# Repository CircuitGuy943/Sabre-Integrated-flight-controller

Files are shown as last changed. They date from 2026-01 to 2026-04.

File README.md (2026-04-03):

I am currently trying to build my own drone from scratch, and slowly replace every component with my own, from creating fully custom PCBs for the flight controller or ESCs, to making a 3D printed drone chassis etc etc. And this is the fully fledged, multi functional, cool-looking flight controller. I present to you:

# *SABRE!*




For one of my biggest projects yet I designed a jack of all trades custom flight controller board. It also comes with custom firmware, or if possible compatibility with betaflight or other FC firmware out there. At it's core are two PCBs arranged in a stackup with the "top" and "bottom" sections. The two PCBs connect through the common 2.54mm pitch headers and stack on top of eachother and each serve to provide enough space for all the components and separate the sensitive digital components from the electromagnetic potential of the motor power rails. The bottom board houses E-Fuse protection and an INA226 current monitor to protect the boards, including powered FPV feed with the AT7456E and TX5813, accompanied by four MOSFET powered 12V LED strip channels. The top booard houses a powerful STM32F765VGT CPU which will, *fingers crossed,* be more than enough to run automatic flight levelling software quickly enough to not crash. Followed by a micro SD card slot for storing flight telemetry, programmable DIP switched for easy settings, BNO08x 9-DOF sensor module, segment display and pushbuttons for easy configuration without needing to reupload code and a BMP580 barometic sensor. More than I (or you) will ever need to fly a 4 blade, 1KG piece of PETG plastic :)

### Bottom Board:

Half of the bottom PCB houses the power delivery circuitry. This includes a dedicated TPS259850 chip, or an E-Fuse, required protection option for a drone that operates at around 20A sustained and 40A current peaks. Thanks to it's extremely low RDS on, basically no power is wasted, and it trips the circuit in a matter of microseconds when too much current is detected, which makes it extremely useful for a drone full of sensitive circuitry, compared to a traditional wire fuse. Followed by that is an INA226 chip, this aims to precisely monitor the current consumption of the entire drone, helping to predict flight times and efficiently manage battery health, through the use of a shunt resistor sized to the expected current draw. The current planes are optimized to make proper use of the different outer and inner layer thicknesses and properly distribute current with minimal heat up.

The other part of the bottom PCB houses the RF circuitry for the FPV system LED drivers togethor with power regulators that power the 12V rail for the LED drivers and the 5V rail for the FPV system and other 5V chips. The 12V power regulator (TPS55289) and the 5V regulator (TPS63070) both use the safest and most reliable layouts possible and are positioned to spatially divide the high ~32A currents on the bottom power distribution circuitry from the rest of the bottom board, a slide switch also controls the power supply to the TX5813 module, as this consumes the most out of the other board circuitry, at about ~200mA, this should help to increase flight time by cutting wasted power when the FPV function isn't being used. CSD16340 MOSFETS also serve to drive 4 seperate 12V LED strip channels, these I plan to connect to LED strips and create cool illuminations off of my drone.

The RF circuitry benefits from an impedance accurate JLC-3313 stackup and use of coplanar waveguide routing with via fencing, tearsrops and udnerpad via router to insure the least impedance mismatch possible. The actual RF system is composed of an external camera connector, or simple pin header (capable of reading almost any FPV camera such as the Caddx Ant Lite). The video signal is then passed through a meticulously routed 75ohm impedance matched trace into a MAX7456EUI (Or a newer drop in AT7456E replacement, pin to pin compatible), this module serves to inject an OSD (On screen display) into the video feed through communication with the STM32 MCU for easy sending of telemtry data like battery voltage, speed, altitude etc. The output from the OSD injection chip is then routed through another impedance matched trace with SAG correction into the video input of the TX5813. This modules handles the complicated circuitry of converting the video feed (~6MHz) into a radio signal of ~5.8GHz. That RF is then routed even more carefuly for the short length (~8mm) of the SMA launch into the SMA connector then into any respective 5.8GHz FPV antenna. (I also have a complemintary project for a 5.8GHz FPV reciever in another repository)

### Top Board:

Flying the drone is an STM32F765VGT CPU with up to 216MHz clock speed, hopefully resulting in almost perfect drone levelling and flight, on the other side of the board is also a USB C receptacle for programming the STM CPU, and powering the board while doing so (everything except the motors, of course, I also included diodes to prevent power backfeed). Close by is a BNO08x 9-DOF accelerometer, gyroscope and magnetometer, complete with an integrated 32-bit ARM Cortex-M0+ for quick sensor fusion with pre built firmware (meaning I have to code waaaay less :D). Motor PWM outputs for the ESCs also connected directly to PWM channels on the STM32 and two solder bridgeable connections to allow me to use the 5V supply from the ESCs in case my 5V regulator doesn't function properly under load (I've had bad experience with voltage regulators). Several voltage indicator LEDs are also placed near the USB C port at the back. Then there is also an UART FPC port designed to connect to a separate GPS board (large board for good GPS recieving power, check my other repositories) on the left side of the board. A 7 segment, 4 digit bitbanged display and several tactile pushbottoms also occupy the centre of the board, quite useless but they might be useful in changing more accute settings without having to reupload firmware every time. A micro SD card also connects through 4 channel SPI to STM32, I plan to use this to store settings or flight telemetry information that I could analyze while debugging. Powering all that is a 3.3V regulator (LMR51430XF), simplest (and therefore most reliable) I could find. And several other breakout headers for power/functionality. PWM inputs from the radio remote is recieved through a 3x8 header pinout designed for my specific radio reciever module.

## Features:
- Fully integrated design:
	- Custom firmware uploadable
	- Power distribution and control in one place
	- Dual stacked PCB design
 	- No screw, no wire inter board connection

- Power
	- Extremely low RDS protection e-Fuse (us trip time)
 	- INA226 current and voltage monitoring
  	- Backup/calibration voltage divider monitoring
  	- Fully optimized current planes, 40A+ capability
  	- Firmware built in battery management and flight warning system
  	- Meticulously designed 5V, 12V and 3.3V switching voltage regulators
  	- Backup ESC 5V supply availible
  	- LED indicators for power rail status
  	- 4 channel driver for 12V LED strips
  	- Power switch for TX5813 module for longer flight times

- Fully integrated FPV support
	- MAX7456/AT7456E OSD injection into FPV feed
	- Channel switch ability
	- TX5813 RF launch module
	- Accurate and reliable RF design
 	- Designed for impedance matched JLC 3313 stackup
 
- Flight Control
	- USB C programming connection 
	- Powerful STM32F765VGT CPU
 	- MicroSD card slot (For inflight telemtry storage)
  	- Programmable DIP switches
  	- Display/pushbuttons for setting adjustment without code reupload
  	- BNO08x 9-DOF sensor module with built in sensor fusion
  	- BMP580 Barometric sensor
  	- UART FPC connection for external GPS board
  	- Extra power and I2C debug headers
  	- 7 input PWM channels
  	- 4 ESC output PWM channels

## PCB
This is the PCB, with L1 to L4 Layers, silkscreen for both layers and an all layers view

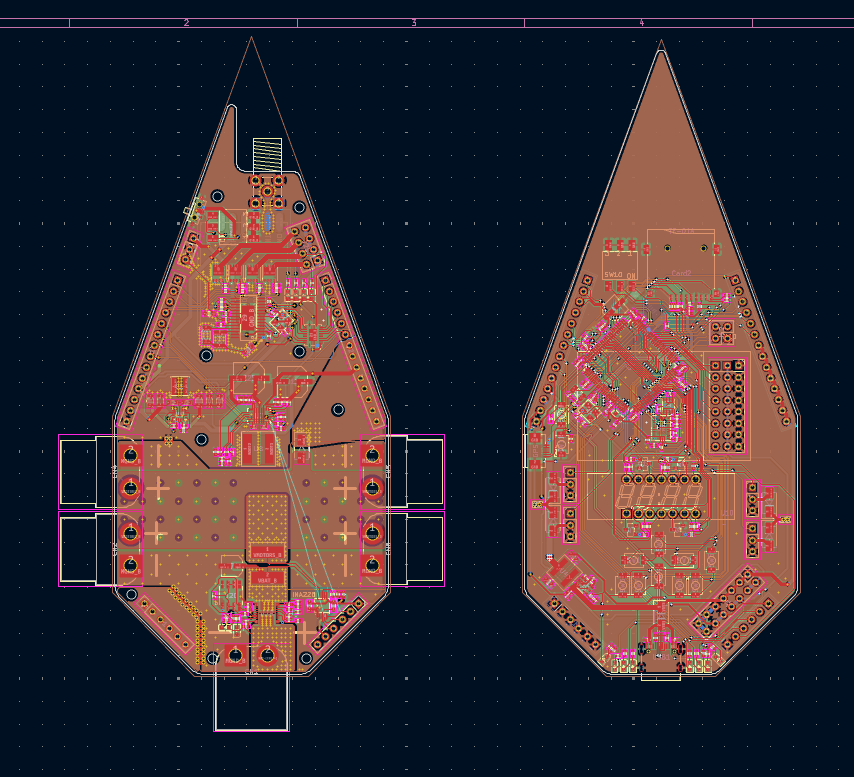
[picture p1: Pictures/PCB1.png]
PCB
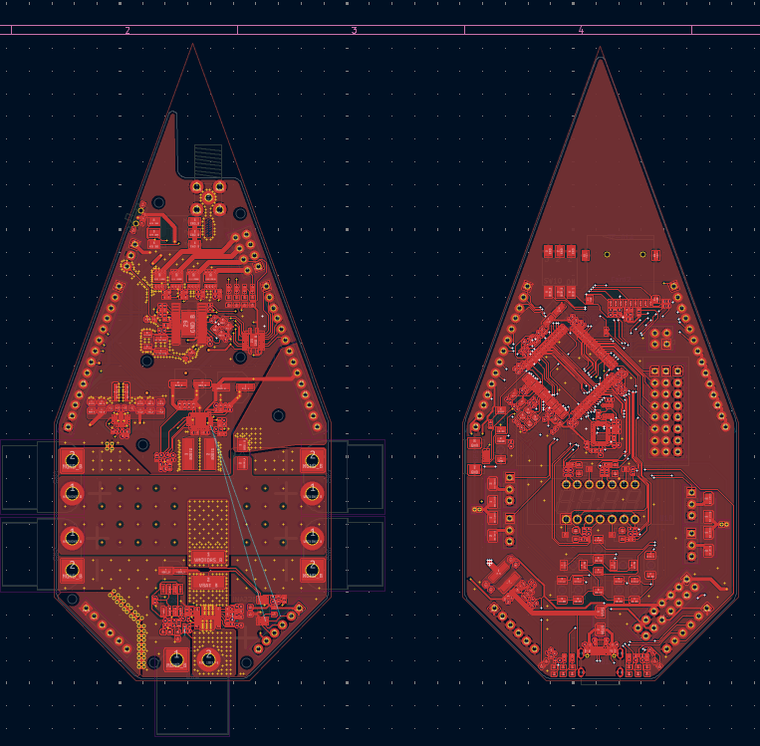
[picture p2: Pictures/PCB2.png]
PCB 2
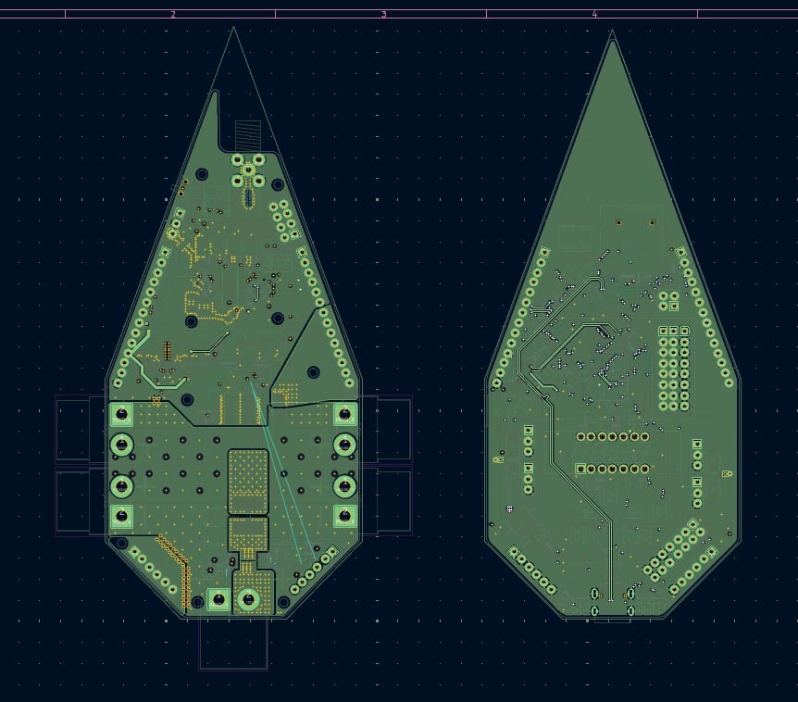
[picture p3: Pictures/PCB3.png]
PCB 3
   
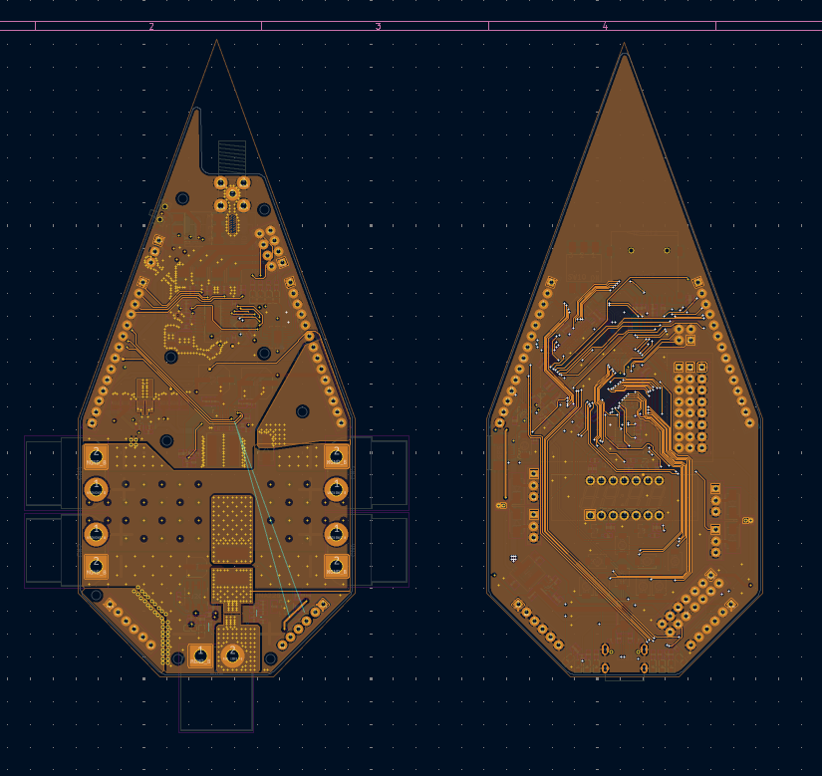
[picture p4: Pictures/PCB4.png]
PCB 4
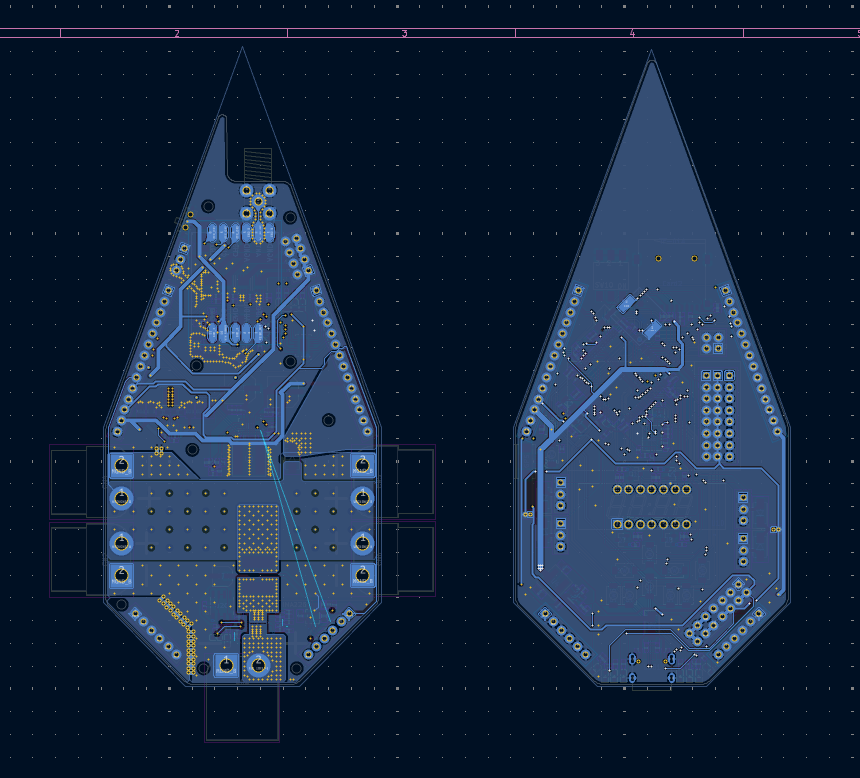
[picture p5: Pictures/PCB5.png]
PCB 5
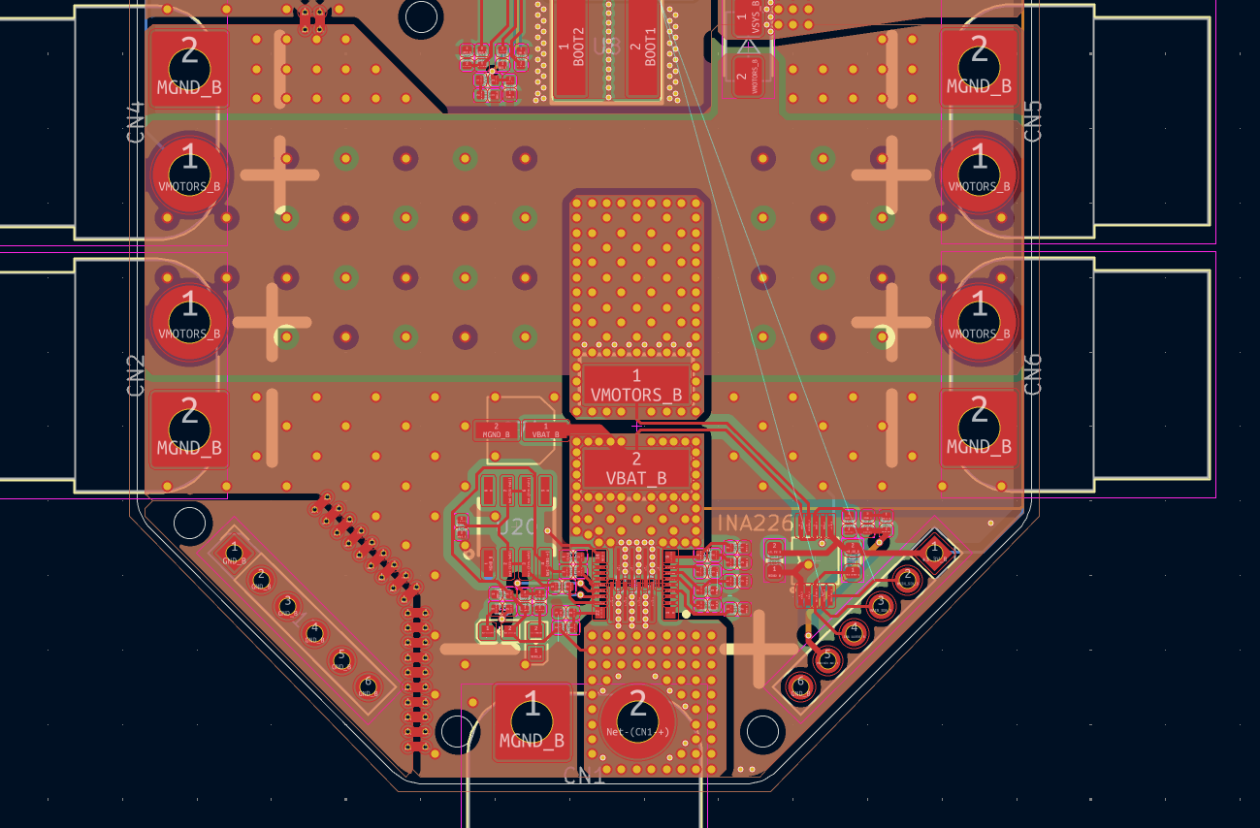
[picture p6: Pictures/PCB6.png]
PCB 6
  
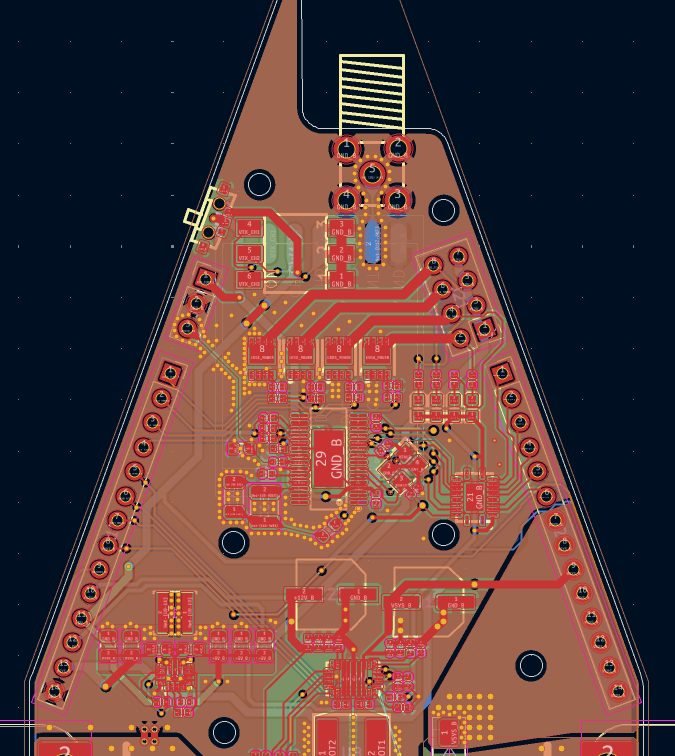
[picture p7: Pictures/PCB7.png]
PCB 7
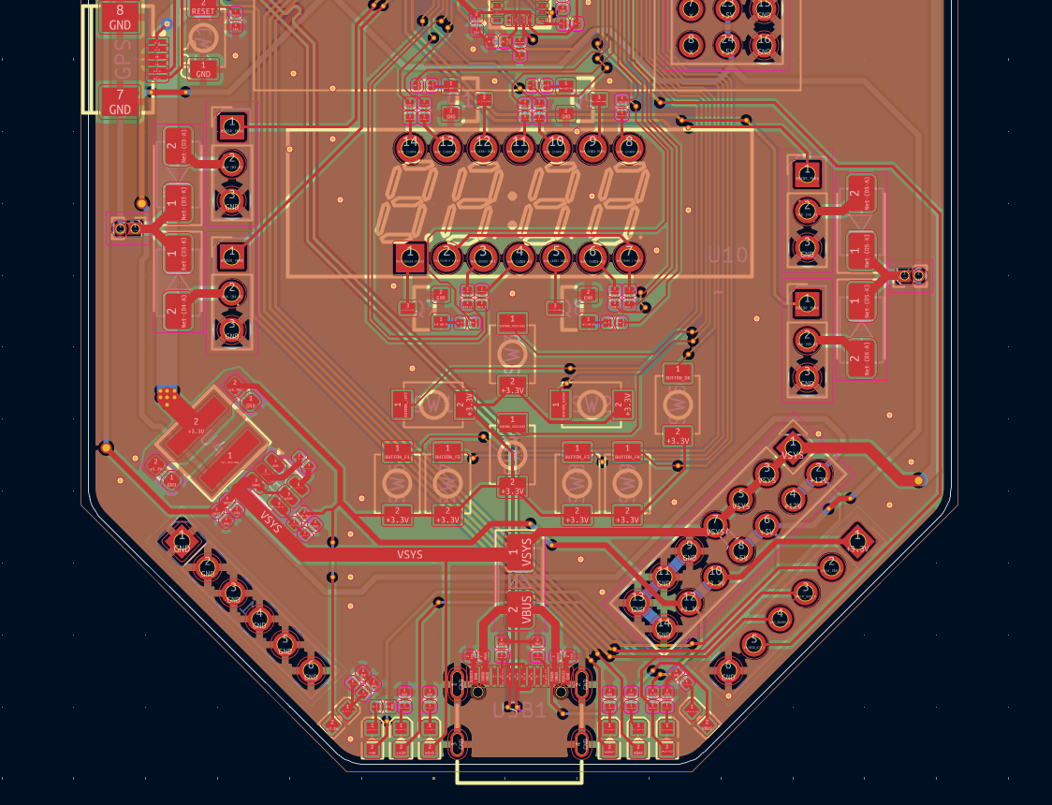
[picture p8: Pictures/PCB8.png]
PCB 8
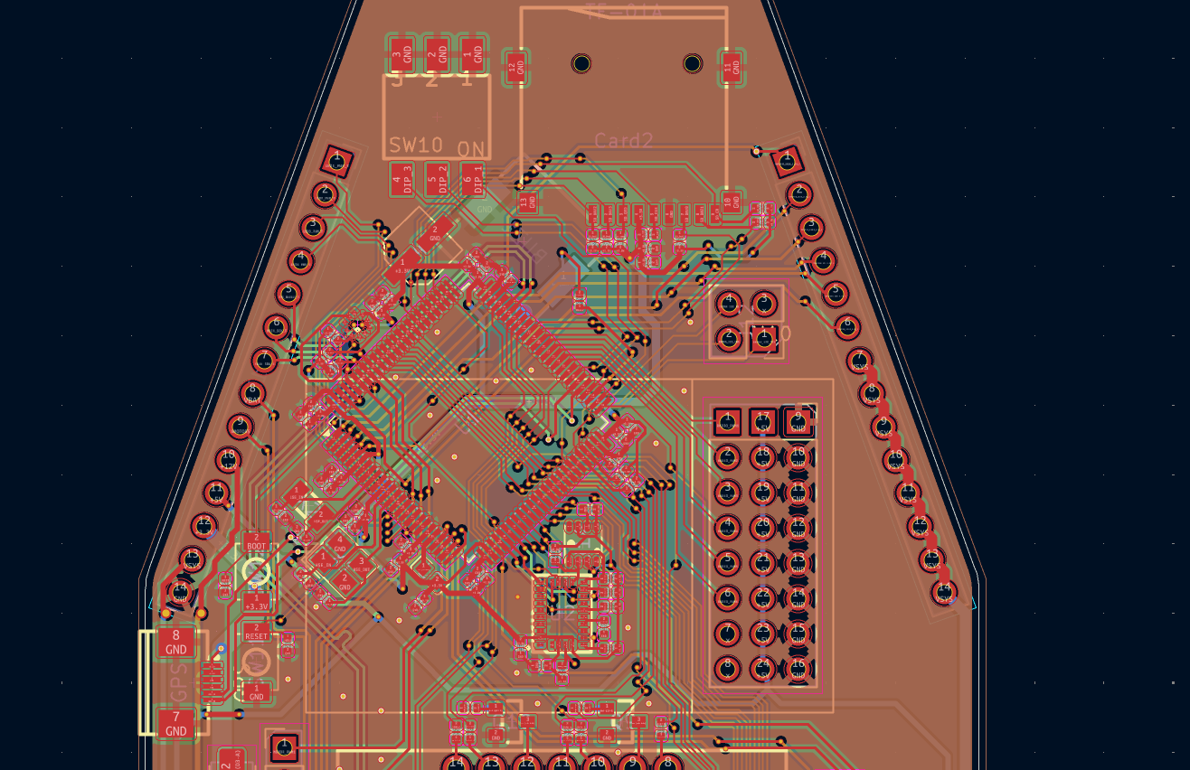
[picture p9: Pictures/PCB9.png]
PCB 9
   

And here is the schematic

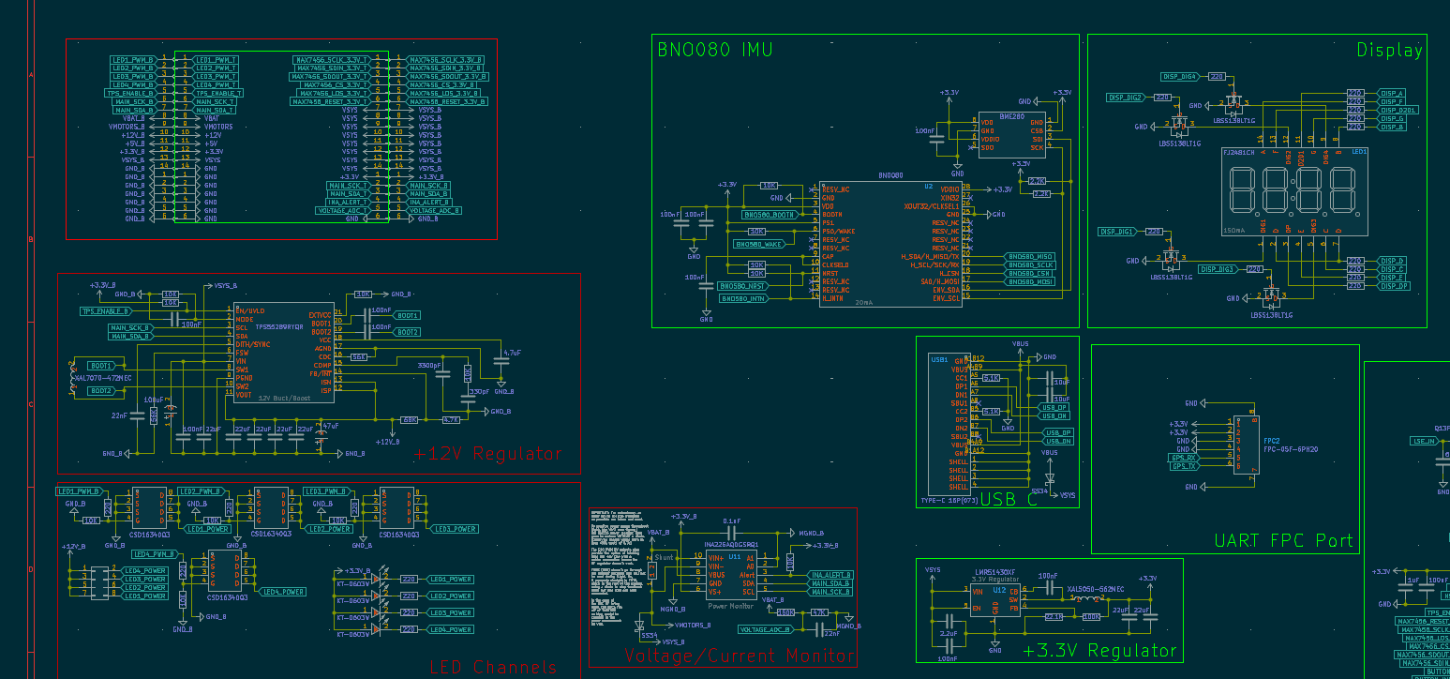
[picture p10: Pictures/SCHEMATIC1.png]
Schematic1

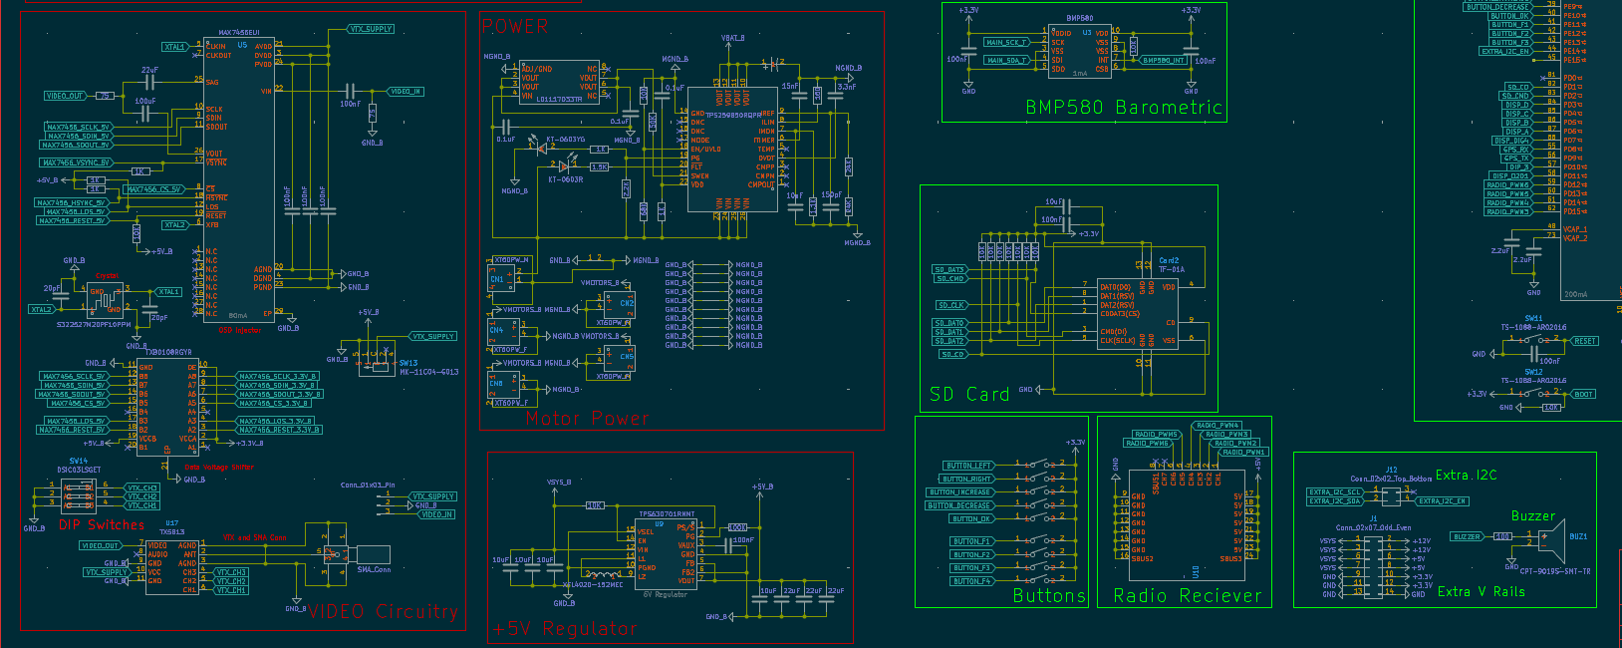
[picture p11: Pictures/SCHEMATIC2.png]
Schematic2

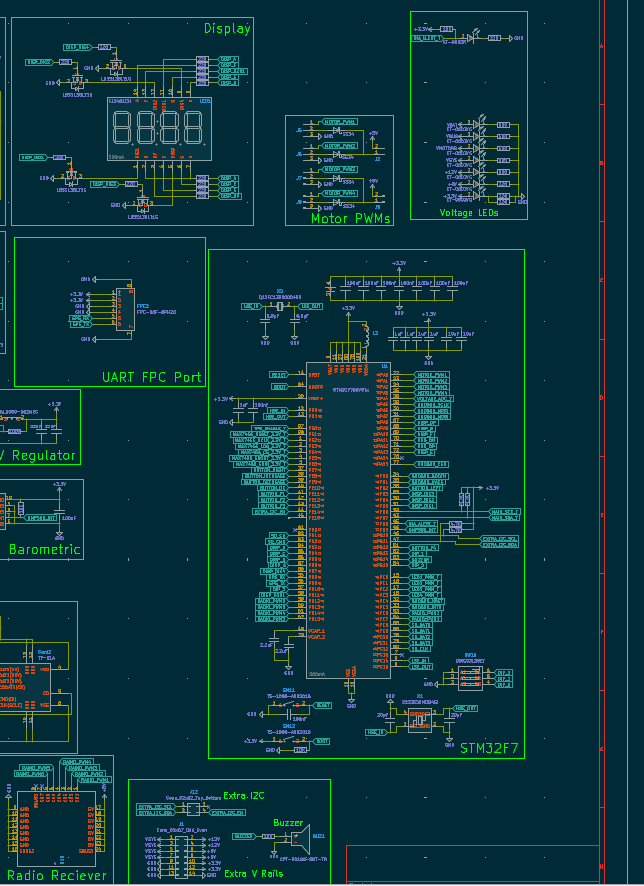
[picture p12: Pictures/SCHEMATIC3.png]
Schematic3


## Firmware Overview
I've included some basic firmware (**untested**) that should get the TFT display working out of the box with a quick upload from arduino IDE

## BOM:
The BOM list for the actual PCB components is in the BOM folder section and here is also a BOM list for all the other components I plan to buy for this:

- PCB             $378.08		
- Antenna         $7.77      https://www.aliexpress.com/item/1005006153683653.html		
- 90 degree SMA   $4.51      https://www.aliexpress.com/item/1005005665998117.html						
- TX5813 module   $15.82     https://www.aliexpress.com/item/1005011698073364.html
											
Total			      $406.18

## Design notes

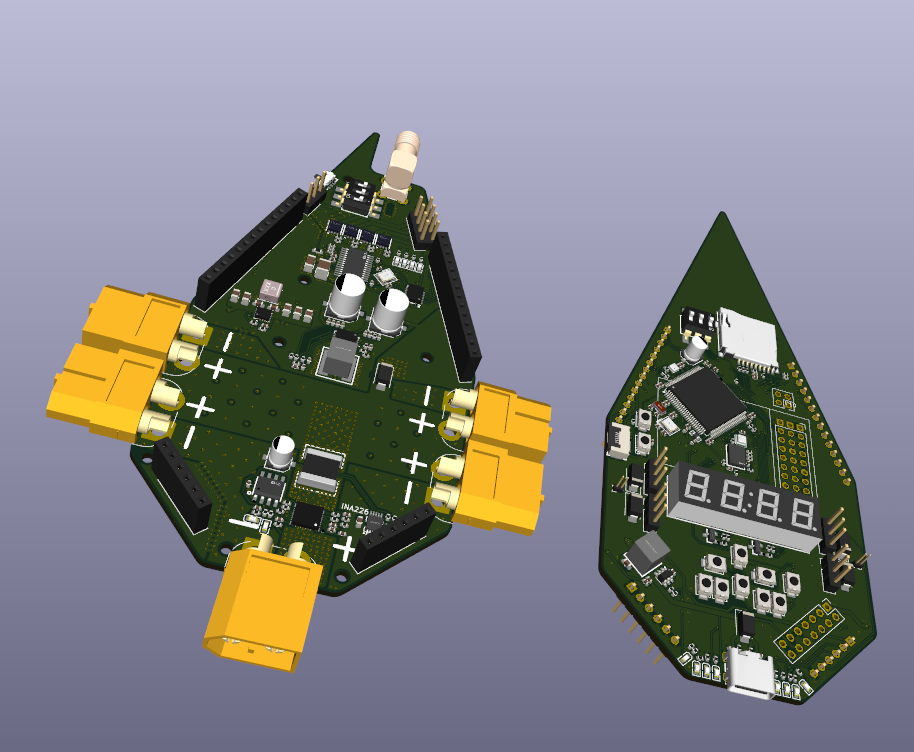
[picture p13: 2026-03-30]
Pictures/RENDER1.png

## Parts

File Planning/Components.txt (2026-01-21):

SENSORS
1. 9 Axis DOF IMU - BNO085. Sensor fusion integrated into the chip, reduces the need for MCU Kalman filters etc and therefore reduces MCU load and increases reliability
2. Barometer for altitude / temperature - BMP580. Can be connected straight to MCU or through a passthrough for “Environmental Sensors” through the BNO085, this is harder to implement but it may simplify circuitry use less I2C lines.
3. STM32 processor. Which one? Needs to be dual core (Update: Doesn't need to be dual core)

CONTROL
1. GPIO PWM outputs connected to 4 (more if there is space) groups of 3 pin headers for the ESCs, backup 5V power will also be taken from here as ESCs also step-down power to 5V. Located preferably in a symmetric position or spread out symmetrically so all the wires are extended the same.
2. PWM Inputs from the Radio Receiver (6 groups of also 3 pin headers, more if there is space and GPIO availability). These must OUTPUT 5V as well because the receiver needs a voltage input to function, unlike the ESCs that make their own.

POWER
1. USB C port connection on the back of the board
2. Female XT60 power connector with appropriate step down for MCU and sensors (Not LDO as components will likely consume too much current for too high a step down from ~14V)
3. Dual connection with diodes to both the ESC power outputs but also a voltage reducer like LDO or buck reducer on the USB C for redundancy if the LDO/buck dies.
4. Each side of the board will also have 2 (Maybe more if there's space) XT60 connectors powering the ESCs/motors

CAMERA SUPPORT
1. Caddx Ant (Lite) camera
2. 75-ohm impedance matched trace from JST-SH 1.0?mm connector to VID_IN of OSD Injector
3. MAX7456 OSD injector connected through communication protocol to MCU
4. MAC7456 VID_OUT connected through another 75-ohm impedance matched trace to TX5813 VID_IN
5. TX5813 SMD VTX + necessary support electronics + switch for on/off as VTX is very power hungry
6. 50-ohm impedance matched / ground trace from ANTENNA pad to an SMA connector
7. Antenna
Plus, appropriate ground plane and distances from other electronics such as MCU and switching regulators

OTHER
1. 12V LED control with up to 200mA+ of power available from GPIO.
2. SD Card module also placed wherever best, far away from the VTX module and preferably close to the MCU
3. I2C and SPI output headers for any future addition of sensors/logging/modules
4. 4 segment display (3 if not enough GPIO) plus a few tactile buttons (again GPIO limited) to allow easy tweaking of PID control values and other settings without the need for reupload of code.
5. Voltage divider for voltage sensing.
6. Voltage and current sensing on main power rail

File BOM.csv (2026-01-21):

Reference | Qty | Value | DNP | Exclude from BOM | Exclude from Board | Footprint | Datasheet | LCSC Part | Description | #
BUZ1 | 1 | CPT-9019S-SMT-TR |  |  |  | LCSC:BUZ-SMD_L9.0-W9.0-P8.00-LS9.3 |  | C95163 |  | 1
C1 | 1 | 0.1uF |  |  |  | Capacitor_SMD:C_0603_1608Metric | ~ |  | Unpolarized capacitor | 2
C2,C11,C14,C15,C26,C27,C29,C30,C31,C32,C33,C34,C36,C37,C38,C41,C44,C45,C46,C47,C48,C49,C50,C51,C63,C64 | 26 | 100nF |  |  |  | Capacitor_SMD:C_0402_1005Metric | ~ |  | Unpolarized capacitor,X7R MLCC 25V | 3
C3,C6 | 2 | 10uF |  |  |  | Capacitor_SMD:C_0603_1608Metric | ~ |  | Unpolarized capacitor | 4
C4,C5 | 2 | 10uF |  |  |  | Capacitor_SMD:C_0805_2012Metric | ~ |  | Unpolarized capacitor,Unpolarized capacitor X7S | 5
C7,C8,C9 | 3 | 22uF |  |  |  | Capacitor_SMD:C_0805_2012Metric | ~ |  | Unpolarized capacitor | 6
C10,C57,C58 | 3 | 2.2uF |  |  |  | Capacitor_SMD:C_0402_1005Metric | ~ |  | Unpolarized capacitor | 7
C12,C13,C16,C19,C20,C21,C22 | 7 | 22uF |  |  |  | Capacitor_SMD:C_0603_1608Metric | ~ |  | Unpolarized capacitor,X7R MLCC 25V | 8
C17 | 1 | 4.7uF |  |  |  | Capacitor_SMD:C_0402_1005Metric | ~ |  | Unpolarized capacitor | 9
C18,C28 | 2 | 22nF |  |  |  | Capacitor_SMD:C_0402_1005Metric | ~ |  | Unpolarized capacitor | 10
C23 | 1 | 3300pF |  |  |  | Capacitor_SMD:C_0402_1005Metric | ~ |  | Unpolarized capacitor | 11
C24 | 1 | 330pF |  |  |  | Capacitor_SMD:C_0402_1005Metric | ~ |  | Unpolarized capacitor | 12
C25 | 1 | 47uF |  |  |  | LCSC:CAP-SMD_BD6.3-L6.6-W6.6-LS7.2-FD |  | C970677 | RVT1E470M0605 25V | 13
C35,C43,C56 | 3 | 10uF |  |  |  | Capacitor_SMD:C_0402_1005Metric | ~ |  | Unpolarized capacitor | 14
C39,C40,C60,C61 | 4 | 20pF |  |  |  | Capacitor_SMD:C_0402_1005Metric | ~ |  | Unpolarized capacitor | 15
C42,C66 | 2 | RVT1C220M0405_C3356_22uF |  |  |  | LCSC:CAP-SMD_BD4.0-L4.3-W4.3-FD-LS5.3 | https://lcsc.com/product-detail/Aluminum-Electrolytic-Capacitors-SMD_22uF-16V_C3356.html | C3356 |  | 16
C52,C53,C54,C55,C65 | 5 | 1uF |  |  |  | Capacitor_SMD:C_0402_1005Metric | ~ |  | Unpolarized capacitor | 17
C59,C62 | 2 | 6.8pF |  |  |  | Capacitor_SMD:C_0402_1005Metric | ~ |  | Unpolarized capacitor | 18
Card1 | 1 | SD-006M |  |  |  | LCSC:SD-SMD_SD-006M | https://lcsc.com/product-detail/Card-Sockets_SDDeck_C125615.html | C125615 | 100mA | 19
CN1 | 1 | XT60PW_M |  |  |  | Connector_AMASS:AMASS_XT60PW-M_1x02_P7.20mm_Horizontal |  | C98732 |  | 20
CN2,CN4,CN5,CN6 | 4 | XT60PW_F |  |  |  | Connector_AMASS:AMASS_XT60PW-F_1x02_P7.20mm_Horizontal |  | C428722 |  | 21
CN3 | 1 | Camera Conn |  |  |  | LCSC:CONN-TH_S3B-ZR-SM4A-TF-LF-SN | https://lcsc.com/product-detail/ZH-Connectors-1-5mm_JST_S3B-ZR-SM4A-TF-LF-SN_ZHseries-socket-1-3P-pitch1-5mm_C72591.html | C72591 |  | 22
D1,D2,D3,D4,D5,D6 | 6 | SS34 |  |  |  | Diode_SMD:D_SMA | https://www.vishay.com/docs/88751/ss32.pdf |  | 40V 3A Schottky Diode, SMA | 23
J1,J2,J3,J4 | 4 | Conn_01x04_Pin |  |  |  | Connector_PinHeader_2.54mm:PinHeader_1x04_P2.54mm_Vertical | ~ |  | +++,--- | 24
J5,J6,J7,J8,J10 | 5 | Conn_01x03_Pin |  |  |  | Connector_PinHeader_2.54mm:PinHeader_1x03_P2.54mm_Vertical | ~ |  | Generic connector, single row, 01x03, script generated | 25
J9 | 1 | Conn_01x02_Pin |  |  |  | Connector_PinHeader_1.00mm:PinHeader_1x02_P1.00mm_Vertical | ~ |  | Generic connector, single row, 01x02, script generated | 26
J11 | 1 | Conn_02x07_Top_Bottom |  |  |  | Connector_PinHeader_2.54mm:PinHeader_2x07_P2.54mm_Vertical | ~ |  | Generic connector, double row, 02x07, top/bottom pin numbering scheme (row 1: 1...pins_per_row, row2: pins_per_row+1 ... num_pins), script generated (kicad-library-utils/schlib/autogen/connector/) | 27
J12 | 1 | Conn_02x02_Top_Bottom |  |  |  | Connector_PinHeader_2.54mm:PinHeader_2x02_P2.54mm_Vertical | ~ |  | Generic connector, double row, 02x02, top/bottom pin numbering scheme (row 1: 1...pins_per_row, row2: pins_per_row+1 ... num_pins), script generated (kicad-library-utils/schlib/autogen/connector/) | 28
J13,J14 | 2 | Conn_01x20_Pin |  |  |  | Connector_PinHeader_2.54mm:PinHeader_1x20_P2.54mm_Vertical | ~ |  | Generic connector, single row, 01x20, script generated | 29
J15,J16 | 2 | Conn_01x20_Socket |  |  |  | Connector_PinSocket_2.54mm:PinSocket_1x20_P2.54mm_Vertical | ~ |  | Generic connector, single row, 01x20, script generated | 30
L1 | 1 | XFL4020-152MEC |  |  |  | LCSC:IND-SMD_L4.0-W4.0-A |  | C3033018 |  | 31
L2 | 1 | FCM1608KF-601T03 |  |  |  | LCSC:L0603 | https://lcsc.com/product-detail/Multilayer-Ceramic-Capacitors_600R-25-at100MHz_C141723.html | C141723 |  | 32
LED1 | 1 | FJ2481CH |  |  |  | LCSC:LED-SEG-TH_14P-L32.2-W10.2-P2.54-S7.62-BL | https://lcsc.com/product-detail/Led-Segment-Display_4Bit0-28Inch-red-digital-LED_C10707.html | C10707 | 150mA | 33
LED2,LED11,LED12,LED13,LED14,LED15,LED16 | 7 | KT-0603YG |  |  |  | LCSC:LED0603-RD | https://lcsc.com/product-detail/Light-Emitting-Diodes-LED_Yellow-green-0603_C2289.html | C2289 |  | 34
LED3 | 1 | KT-0603R |  |  |  | LCSC:LED0603-RD | https://lcsc.com/product-detail/Light-Emitting-Diodes-LED_Red-LED-0603_C2286.html | C2286 |  | 35
LED4,LED5,LED6,LED7 | 4 | KT-0603W |  |  |  | LCSC:LED0603-R-RD_WHITE | https://lcsc.com/product-detail/Light-Emitting-Diodes-LED_0603White-light_C2290.html | C2290 |  | 36
NT1 | 1 | NetTie_4 |  | Excluded from BOM |  | NetTie:NetTie-4_THT_Pad1.0mm | ~ |  | Net tie, 4 pins | 37
NT2 | 1 | NetTie_2 |  | Excluded from BOM |  | NetTie:NetTie-2_THT_Pad1.0mm | ~ |  | Net tie, 2 pins | 38
P1 | 1 | WJ127-5.0-2P |  |  |  | LCSC:CONN-TH_2P-P5.00_CPC3703CTR | https://lcsc.com/product-detail/Terminal-Blocks_WJ127-5-0-2P_C3703.html | C3703 |  | 39
Q1,Q2,Q3,Q5 | 4 | CSD16340Q3 |  |  |  | LCSC:VSON-CLIP-8_L3.3-W3.3-P0.65-BL | https://lcsc.com/product-detail/MOSFET_TI_CSD16340Q3_CSD16340Q3_C47616.html | C47616 |  | 40
Q7,Q8,Q9,Q10 | 4 | LBSS138LT1G |  |  |  | LCSC:SOT-23_L2.9-W1.3-P1.90-LS2.4-BR | https://lcsc.com/product-detail/MOSFET_LBSS138LT1G_C8490.html | C8490 |  | 41
R1,R2 | 2 | 5.1K |  |  |  | Resistor_SMD:R_0402_1005Metric | ~ |  | Resistor | 42
R3 | 1 | HOLR2725D-4W-2MR-1% |  |  |  | LCSC:R2725 | https://lcsc.com/product-detail/Low-Resistors-Current-Sense-Resistors-Surface-Mount_Milliohm-HoLR2725D-4W-2mR-1_C500746.html | C500746 | Shunt | 43
R4,R17,R18,R19,R21,R36,R37,R38,R39,R40,R41,R42,R43,R44,R45,R46,R47,R48,R60,R67,R68,R69,R76,R77,R82 | 25 | 220 |  |  |  | Resistor_SMD:R_0402_1005Metric | ~ |  | Resistor | 44
R5,R72,R73,R74,R75 | 5 | 680 |  |  |  | Resistor_SMD:R_0402_1005Metric | ~ |  | Resistor | 45
R6,R7,R12,R20,R22,R27,R28,R29,R30,R31,R34,R35,R49,R50,R51,R52,R53,R54,R55,R56,R57,R58,R59,R61,R62,R63,R64,R65,R66,R88,R89,R90,R91,R92,R93,R94,R95,R96,R97,R98,R102 | 41 | 10K |  |  |  | Resistor_SMD:R_0402_1005Metric | ~ |  | Resistor | 46
R8,R9 | 2 | 100K |  |  |  | Resistor_SMD:R_0402_1005Metric | ~ |  | Resistor | 47
R10 | 1 | 22.1K |  |  |  | Resistor_SMD:R_0402_1005Metric | ~ |  | Resistor | 48
R11 | 1 | 68K |  |  |  | Resistor_SMD:R_0402_1005Metric | ~ |  | Resistor | 49
R13,R14 | 2 | 56K |  |  |  | Resistor_SMD:R_0402_1005Metric | ~ |  | Resistor | 50
R15 | 1 | MS122WF100MT4E |  |  |  | LCSC:R2512 | https://lcsc.com/product-detail/Metal-Alloy-Resistors_0-01R-R010-1_C68609.html | C68609 |  | 51
R16,R99,R100,R103,R104 | 5 | 4.7K |  |  |  | Resistor_SMD:R_0402_1005Metric | ~ |  | Resistor | 52
R23 | 1 | 150K |  |  |  | Resistor_SMD:R_0603_1608Metric | ~ |  | Resistor | 53
R24 | 1 | 47K |  |  |  | Resistor_SMD:R_0603_1608Metric | ~ |  | Resistor | 54
R25,R26 | 2 | 2.2K |  |  |  | Resistor_SMD:R_0402_1005Metric | ~ |  | Resistor | 55
R78 | 1 | 100 |  |  |  | Resistor_SMD:R_0402_1005Metric | ~ |  | Resistor | 56
R83,R84 | 2 | 75 |  |  |  | Resistor_SMD:R_0603_1608Metric | ~ |  | Resistor | 57
R85,R86,R87 | 3 | 1K |  |  |  | Resistor_SMD:R_0402_1005Metric | ~ |  | Resistor | 58
R101 | 1 | 10K |  |  |  | Resistor_SMD:R_0603_1608Metric | ~ |  | Resistor | 59
SW1,SW2,SW3,SW4,SW5,SW6,SW7,SW8,SW9,SW11,SW12 | 11 | TS-1088-AR02016 |  |  |  | LCSC:SW-SMD_L3.9-W3.0-P4.45 | https://lcsc.com/product-detail/Tactile-Switches_XUNPU-TS-1088-AR02016_C720477.html | C720477 |  | 60
SW10 | 1 | DSIC10LSGET |  |  |  | LCSC:SW-SMD_20P-L26.4-W6.2-P2.54-LS9.8 | https://lcsc.com/product-detail/DIP-Switches_2-54mm-10-DIP-switch_C54954.html | C54954 |  | 61
SW13 | 1 | MK-11C04-G013 |  |  |  | LCSC:SW-SMD_MK-11C04-G013 | https://lcsc.com/product-detail/Toggle-Switches_G-Switch-MK-11C04-G013_C778185.html | C778185 |  | 62
U1 | 1 | STM32F765VGTx |  |  |  | Package_QFP:LQFP-100_14x14mm_P0.5mm | https://www.st.com/resource/en/datasheet/stm32f765vg.pdf |  | 200mA | 63
U2 | 1 | BNO080 |  |  |  | LCSC:LGA-28_L5.2-W3.8-P0.50-BL-1 |  | C717991 | 20mA | 64
U3 | 1 | BMP580 |  |  |  | LCSC:LGA-10_L2.0-W2.0-P0.50-TL_BMP580 |  | C22391138 | 1mA | 65
U4 | 1 | XAL5050-562MEC |  |  |  | LCSC:IND-SMD_L5.5-W5.3 |  | C7305309 |  | 66
U5 | 1 | MAX7456EUI |  |  |  | LCSC:HTSSOP-28_L9.7-W4.4-P0.65-LS6.4-BL-EP5.5 |  | C5346361 | 80mA | 67
U6 | 1 | SMA_Conn |  |  |  | LCSC:SMA-TH_SMA-KWE_C7498154 |  | C7498154 |  | 68
U7 | 1 | TPS55289RYQR |  |  |  | LCSC:VQFN-21_L5.0-W3.0-P0.50-TL |  | C5942077 | 12V Buck/Boost | 69
U8 | 1 | XAL7070-472MEC |  |  |  | LCSC:IND-SMD_L7.5-W7.2-1 |  | C3911513 |  | 70
U9 | 1 | TPS630701RNMT |  |  |  | LCSC:VQFN-15_L3.0-W2.5-P0.50-BL | https://lcsc.com/product-detail/DC-DC-Converters_TI_TPS630701RNMT_TPS630701RNMT_C181473.html | C181473 | 5V Regulator | 71
U10 | 1 | ~ |  |  |  | my:MC7RE |  |  | MC7REV2 compatible female pin headers for direct PCB connection | 72
U11 | 1 | INA226AQDGSRQ1 |  |  |  | LCSC:VSSOP-10_L3.0-W3.0-P0.50-LS4.9-BL |  | C2653835 | Power Monitor | 73
U12 | 1 | LMR51430 |  |  |  | Package_TO_SOT_SMD:SOT-23-6 | https://www.ti.com/lit/ds/symlink/lmr51430.pdf |  | 3.3V Regulator | 74
U13,U18 | 2 | 100uF |  |  |  | LCSC:CAP-SMD_BD6.3-L6.6-W6.6-LS7.2-FD-1 |  | C970685 | RVT1E101M0607 25V | 75
U14 | 1 | BME280 |  |  |  | LCSC:LGA-8_BME280_BL | https://lcsc.com/product-detail/Sensors_Bosch_BME280_BME280_C92489.html | C92489 |  | 76
U15 | 1 | S322527M20PF10PPM |  |  |  | LCSC:CRYSTAL-SMD_4P-L3.2-W2.5-BL |  | C7420779 |  | 77
U16 | 1 | TXB0108RGYR |  |  |  | LCSC:VQFN-20_L4.5-W3.5-P0.50-BL-EP | https://lcsc.com/product-detail/_Texas-Instruments_TXB0108RGYR_Texas-Instruments-Texas-Instruments-TXB0108RGYR_C194701.html | C194701 |  | 78
U17 | 1 | TX5813 |  |  |  | my:TX5813 |  |  |  | 79
USB1 | 1 | TYPE-C 16P(073) |  |  |  | LCSC:USB-C-SMD_TYPE-C16PIN_C668624 | https://lcsc.com/product-detail/USB-Connectors_SHOU-HAN-TYPE-C-16P-073_C668624.html | C668624 |  | 80
X1 | 1 | X322525MOB4SI |  |  |  | LCSC:CRYSTAL-SMD_4P-L3.2-W2.5-BL | https://lcsc.com/product-detail/SMD-Crystals_YSX321SL-25MHZ-12PF-10PPM-40-85_C9006.html | C9006 |  | 81
X2 | 1 | Q13FC1350000400 |  |  |  | LCSC:FC-135R_L3.2-W1.5 | https://lcsc.com/product-detail/SMD-Crystals_EPSON_Q13FC1350000400_32-768KHz-20ppm-12-5pF_C32346.html | C32346 |  | 82

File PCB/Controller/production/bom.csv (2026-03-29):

Designator | Footprint | Quantity | Value | LCSC Part #
BUZ1 | BUZ-SMD_L9.0-W9.0-P8.00-LS9.3 | 1 | CPT-9019S-SMT-TR | C95163
C1 | 0603 | 1 | 0.1uF
C10, C57, C58 | 0402 | 3 | 2.2uF
C11, C14, C15, C2, C26, C27, C29, C30, C31, C32, C33, C34, C36, C37, C38, C41, C44, C45, C46, C47, C48, C49, C50, C51, C63, C64, C67, C78 | 0402 | 28 | 100nF
C12, C13 | 0603 | 2 | 22uF
C16, C19, C20, C21, C22 | 0402 | 5 | 22uF
C17 | 0402 | 1 | 4.7uF
C18, C28 | 0402 | 2 | 22nF
C23 | 0402 | 1 | 3300pF
C24 | 0402 | 1 | 330pF
C25 | CAP-SMD_BD6.3-L6.6-W6.6-LS7.2-FD | 1 | 47uF | C970677
C3, C6 | 0603 | 2 | 10uF
C35, C43, C56, C68, C77 | 0402 | 5 | 10uF
C39, C40, C60, C61 | 0402 | 4 | 20pF
C4, C5 | 0805 | 2 | 10uF
C42, C66, C74 | CAP-SMD_BD4.0-L4.3-W4.3-FD-LS5.3 | 3 | RVT1C220M0405_C3356_22uF | C3356
C52, C53, C54, C55, C65 | 0402 | 5 | 1uF
C59, C62 | 0402 | 2 | 6.8pF
C69, C75, C76 | 0402 | 3 | 0.1uF
C7, C8, C9 | 0805 | 3 | 22uF
C70 | 0402 | 1 | 15nF
C71 | 0402 | 1 | 3.3nF
C72 | 0402 | 1 | 10nF
C73 | 0402 | 1 | 150pF
CARD2 | TF-SMD_TF-01A | 1 | TF-01A | C91145
CN1 | AMASS_XT60PW-M_1x02_P7.20mm_Horizontal | 1 | XT60PW_M | C98732
CN2, CN4, CN5, CN6 | AMASS_XT60PW-F_1x02_P7.20mm_Horizontal | 4 | XT60PW_F | C428722
D1, D2, D3, D4, D5, D6 | D_SMA | 6 | SS34
J1 | PinHeader_2x07_P2.54mm_Vertical | 1 | Conn_02x07_Odd_Even
J10, J5, J6, J7, J8 | PinHeader_1x03_P2.54mm_Vertical | 5 | Conn_01x03_Pin
J12 | PinHeader_2x02_P2.54mm_Vertical | 1 | Conn_02x02_Top_Bottom
J13, J18 | PinHeader_1x14_P2.54mm_Vertical | 2 | Conn_01x14_Pin
J14, J19 | PinHeader_1x06_P2.54mm_Vertical | 2 | Conn_01x06_Pin
J15, J20 | PinSocket_1x14_P2.54mm_Vertical | 2 | Conn_01x14_Socket
J16, J17 | PinSocket_1x06_P2.54mm_Vertical | 2 | Conn_01x06_Socket
J2, J9 | PinHeader_1x02_P1.00mm_Vertical | 2 | Conn_01x02_Pin
J21 | PinHeader_2x04_P2.54mm_Vertical | 1 | Conn_02x04_Odd_Even
L1 | IND-SMD_L4.0-W4.0-A | 1 | XFL4020-152MEC | C3033018
L2 | L0603 | 1 | FCM1608KF-601T03 | C141723
LED1 | LED-SEG-TH_14P-L32.2-W10.2-P2.54-S7.62-BL | 1 | FJ2481CH | C10707
LED11, LED12, LED13, LED14, LED15, LED16, LED2, LED9 | LED0603-RD | 8 | KT-0603YG | C2289
LED3, LED8 | LED0603-RD | 2 | KT-0603R | C2286
LED4, LED5, LED6, LED7 | LED0603-R-RD_WHITE | 4 | KT-0603W | C2290
Q1, Q2, Q3, Q5 | VSON-CLIP-8_L3.3-W3.3-P0.65-BL | 4 | CSD16340Q3 | C47616
Q10, Q7, Q8, Q9 | SOT-23_L2.9-W1.3-P1.90-LS2.4-BR | 4 | LBSS138LT1G | C8490
R1, R2 | 0402 | 2 | 5.1K
R10 | 0402 | 1 | 22.1K
R100, R103, R104, R16, R99 | 0402 | 5 | 4.7K
R101 | 0603 | 1 | 10K
R102, R12, R20, R22, R27, R28, R29, R30, R31, R34, R35, R49, R58, R6, R61, R62, R63, R64, R65, R66, R7, R88, R96, R97, R98 | 0402 | 25 | 10K
R11, R33 | 0402 | 2 | 68K
R13, R14 | 0402 | 2 | 56K
R15 | R2512 | 1 | MS122WF100MT4E | C68609
R17, R18, R19, R21, R36, R37, R38, R39, R4, R40, R41, R42, R43, R44, R45, R46, R47, R48, R60, R67, R68, R69, R76, R77, R82 | 0402 | 25 | 220
R23 | 0402 | 1 | 150K
R24 | 0402 | 1 | 47K
R25, R26, R55 | 0402 | 3 | 2.2K
R3 | R2725 | 1 | HOLR2725D-4W-2MR-1% | C500746
R32, R54, R85, R86, R87 | 0402 | 5 | 1K
R5, R72, R73, R74, R75 | 0402 | 5 | 680
R50 | 0402 | 1 | 160
R51 | 0402 | 1 | 1.1K
R52 | 0402 | 1 | 48K
R53 | 0402 | 1 | 1.5K
R56 | 0402 | 1 | 50K
R78 | 0402 | 1 | 100
R8, R9 | 0402 | 2 | 100K
R83, R84 | 0603 | 2 | 75
SW1, SW11, SW12, SW2, SW3, SW4, SW5, SW6, SW7, SW8, SW9 | SW-SMD_L3.9-W3.0-P4.45 | 11 | TS-1088-AR02016 | C720477
SW10, SW14 | SW-SMD_DSIC03LSGET | 2 | DSIC03LSGET | C57453
SW13 | SW-SMD_MK-11C04-G013 | 1 | MK-11C04-G013 | C778185
U1 | LQFP-100_14x14mm_P0.5mm | 1 | STM32F765VGTx
U10 | MC7RE | 1 | ~
U11 | VSSOP-10_L3.0-W3.0-P0.50-LS4.9-BL | 1 | INA226AQDGSRQ1 | C2653835
U12 | SOT-23-6 | 1 | LMR51430XF
U13, U18 | CAP-SMD_BD6.3-L6.6-W6.6-LS7.2-FD-1 | 2 | 100uF | C970685
U14 | LGA-8_BME280_BL | 1 | BME280 | C92489
U15 | CRYSTAL-SMD_4P-L3.2-W2.5-BL | 1 | S322527M20PF10PPM | C7420779
U16 | VQFN-20_L4.5-W3.5-P0.50-BL-EP | 1 | TXB0108RGYR | C194701
U17 | TX5813 | 1 | TX5813
U19 | QFN-26_L5.0-W4.5_TPS259850RQPR | 1 | TPS259850RQPR | C6290347
U2 | LGA-28_L5.2-W3.8-P0.50-BL-1 | 1 | BNO080 | C717991
U20 | SO-8_L4.9-W3.9-P1.27-LS6.0-BL | 1 | LD1117D33TR | C2971297
U3 | LGA-10_L2.0-W2.0-P0.50-TL_BMP580 | 1 | BMP580 | C22391138
U4 | IND-SMD_L5.5-W5.3 | 1 | XAL5050-562MEC | C7305309
U5 | HTSSOP-28_L9.7-W4.4-P0.65-LS6.4-BL-EP5.5 | 1 | MAX7456EUI | C5346361
U6 | SMA-TH_SMA-KWE_C7498154 | 1 | SMA_Conn | C7498154
U7 | VQFN-21_L5.0-W3.0-P0.50-TL | 1 | TPS55289RYQR | C5942077
U8 | IND-SMD_L7.5-W7.2-1 | 1 | XAL7070-472MEC | C3911513
U9 | VQFN-15_L3.0-W2.5-P0.50-BL | 1 | TPS630701RNMT | C181473
USB1 | USB-C-SMD_TYPE-C16PIN_C668624 | 1 | TYPE-C 16P(073) | C668624
X1 | CRYSTAL-SMD_4P-L3.2-W2.5-BL | 1 | X322525MOB4SI | C9006
X2 | FC-135R_L3.2-W1.5 | 1 | Q13FC1350000400 | C32346

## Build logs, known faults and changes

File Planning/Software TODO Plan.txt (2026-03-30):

1. Add sensor soft reset for recovery of communication (BMP580 and others)
3. Add battery health management system in program (monitor current across voltage decrease)
5. Adaptive PID and vibration sensing. Log RPM and IMU data

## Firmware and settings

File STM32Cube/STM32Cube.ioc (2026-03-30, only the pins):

Mcu.UserName=STM32F765VGTx
PA0/WKUP.GPIO_Label=MOTOR1
PA0/WKUP.Signal=S_TIM2_CH1_ETR
PA1.GPIO_Label=MOTOR2
PA1.Signal=S_TIM2_CH2
PA10.GPIO_Label=DISP_F
PA10.Signal=GPIO_Output
PA11.Signal=USB_OTG_FS_DM
PA12.Signal=USB_OTG_FS_DP
PA13.GPIO_Label=DISP_E
PA13.Signal=GPIO_Output
PA15.GPIO_Label=BNO_NSS
PA15.Signal=SPI1_NSS
PA2.GPIO_Label=MOTOR3
PA2.Signal=S_TIM2_CH3
PA3.GPIO_Label=MOTOR3
PA3.Signal=S_TIM2_CH4
PA4.GPIO_Label=VOLTAGE_DIVIDER
PA4.Signal=ADCx_IN4
PA5.GPIO_Label=BNO_SCK
PA5.Signal=SPI1_SCK
PA6.GPIO_Label=BNO_MISO
PA6.Signal=SPI1_MISO
PA7.GPIO_Label=BNO_MOSI
PA7.Signal=SPI1_MOSI
PA8.GPIO_Label=DISP_DP
PA8.Signal=GPIO_Output
PA9.GPIO_Label=DISP_G
PA9.Signal=GPIO_Output
PB0.GPIO_Label=BNO_BOOTN
PB0.Signal=GPIO_Output
PB1.GPIO_Label=BNO_WAKE
PB1.Signal=GPIO_Output
PB10.GPIO_Label=EXTRA_I2C_SCL
PB10.Signal=I2C2_SCL
PB11.GPIO_Label=EXTRA_I2C_SDA
PB11.Signal=I2C2_SDA
PB12.GPIO_Label=BUTTON_F4
PB12.Signal=GPIO_Input
PB13.GPIO_Label=DIP_CH1
PB13.Signal=GPIO_Input
PB14.GPIO_Label=BUZZER_PWM
PB14.Signal=S_TIM12_CH1
PB15.GPIO_Label=DIP_CH2
PB15.Signal=GPIO_Input
PB2.GPIO_Label=BUTTON_LEFT
PB2.Signal=GPIO_Input
PB3.GPIO_Label=DISP_DIG3
PB3.Signal=GPIO_Output
PB4.GPIO_Label=DISP_DIG2
PB4.Signal=GPIO_Output
PB5.GPIO_Label=DISP_DIG1
PB5.Signal=GPIO_Output
PB6.GPIO_Label=MAIN_I2C_SCL
PB6.Signal=I2C1_SCL
PB7.GPIO_Label=MAIN_I2C_SDA
PB7.Signal=I2C1_SDA
PB8.GPIO_Label=INA_ALERT
PB8.Signal=GPXTI8
PB9.GPIO_Label=BMP_INT
PB9.Signal=GPXTI9
PC0.GPIO_Label=LEDSTRIP_PWM_1
PC0.Signal=GPIO_Output
PC1.GPIO_Label=LEDSTRIP_PWM_2
PC1.Signal=GPIO_Output
PC10.Signal=SDMMC1_D2
PC11.Signal=SDMMC1_D3
PC12.Signal=SDMMC1_CK
PC14/OSC32_IN.Signal=RCC_OSC32_IN
PC15/OSC32_OUT.Signal=RCC_OSC32_OUT
PC2.GPIO_Label=LEDSTRIP_PWM_3
PC2.Signal=GPIO_Output
PC3.GPIO_Label=LEDSTRIP_PWM_4
PC3.Signal=GPIO_Output
PC4.GPIO_Label=BNO_NRST
PC4.Signal=GPIO_Output
PC5.GPIO_Label=BNO_INTN
PC5.Signal=GPXTI5
PC6.GPIO_Label=RADIO_C2
PC6.Signal=S_TIM3_CH1
PC7.GPIO_Label=RADIO_C1
PC7.Signal=S_TIM3_CH2
PC8.Signal=SDMMC1_D0
PC9.Signal=SDMMC1_D1
PD1.GPIO_Label=SD_CD
PD1.Signal=GPIO_Input
PD10.GPIO_Label=DIP_CH3
PD10.Signal=GPIO_Input
PD11.GPIO_Label=DISP_D2D1
PD11.Signal=GPIO_Output
PD12.GPIO_Label=RADIO_C6
PD12.Signal=S_TIM4_CH1
PD13.GPIO_Label=RADIO_C5
PD13.Signal=S_TIM4_CH2
PD14.GPIO_Label=RADIO_C4
PD14.Signal=S_TIM4_CH3
PD15.GPIO_Label=RADIO_C3
PD15.Signal=S_TIM4_CH4
PD2.Signal=SDMMC1_CMD
PD3.GPIO_Label=DISP_D
PD3.Signal=GPIO_Output
PD4.GPIO_Label=DISP_C
PD4.Signal=GPIO_Output
PD5.GPIO_Label=DISP_B
PD5.Signal=GPIO_Output
PD6.GPIO_Label=DISP_A
PD6.Signal=GPIO_Output
PD7.GPIO_Label=DISP_DIG4
PD7.Signal=GPIO_Output
PD8.Signal=USART3_TX
PD9.Signal=USART3_RX
PE0.GPIO_Label=TPS55289_ENABLE
PE0.Signal=GPIO_Output
PE1.GPIO_Label=MAX_RESET
PE1.Signal=GPIO_Output
PE10.GPIO_Label=BUTTON_OK
PE10.Signal=GPIO_Input
PE11.GPIO_Label=BUTTON_F1
PE11.Signal=GPIO_Input
PE12.GPIO_Label=BUTTON_F2
PE12.Signal=GPIO_Input
PE13.GPIO_Label=BUTTON_F3
PE13.Signal=GPIO_Input
PE14.GPIO_Label=EXTRA_I2C_ENABLE
PE14.Signal=GPIO_Output
PE2.GPIO_Label=MAX_SCK
PE2.Signal=SPI4_SCK
PE3.GPIO_Label=MAX_LOS
PE3.Signal=GPIO_Input
PE4.GPIO_Label=MAX_CS
PE4.Signal=SPI4_NSS
PE5.GPIO_Label=MAX_MISO
PE5.Signal=SPI4_MISO
PE6.GPIO_Label=MAX_MOSI
PE6.Signal=SPI4_MOSI
PE7.GPIO_Label=BUTTON_RIGHT
PE7.Signal=GPIO_Input
PE8.GPIO_Label=BUTTON_INCREASE
PE8.Signal=GPIO_Input
PE9.GPIO_Label=BUTTON_DECREASE
PE9.Signal=GPIO_Input
PH0/OSC_IN.Signal=RCC_OSC_IN
PH1/OSC_OUT.Signal=RCC_OSC_OUT
